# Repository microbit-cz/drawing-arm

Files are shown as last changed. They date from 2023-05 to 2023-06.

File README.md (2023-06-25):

## Language



Thingiverse: https://www.thingiverse.com/thing:6087701
Printables: https://www.printables.com/model/509500-microbit-robotic-drawing-arm-stardraw-megalink

# StardrawMegalink - Robotic drawing arm :tokyo_tower::mechanical_arm::clamp:

<div>
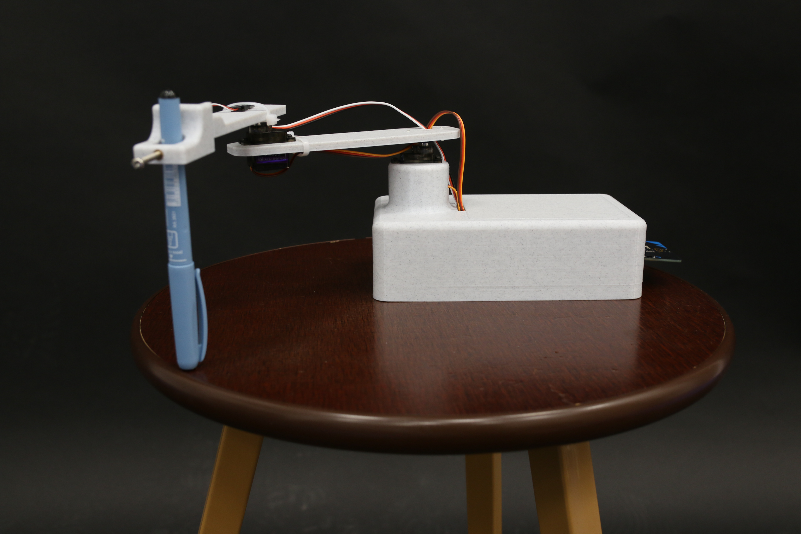
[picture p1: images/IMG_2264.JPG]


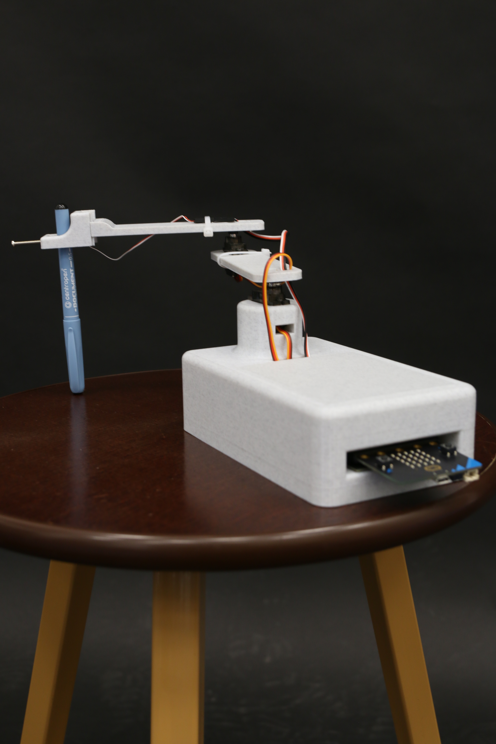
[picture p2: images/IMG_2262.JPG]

</div>

## Content

- [Introduction](#Introduction)
- [Equipment needed and price](#Equipment-needed)
- [Assembly and Printing](#Composition)
- [Software](#Software)

## Introduction
The project aims to create an experimental prototype of a drawing arm with a base. It is designed to test inverse kinematics. The software part is provided by a Micro:bit microcomputer with a library actually written for the digital servos controlling the arms.

## Equipment needed and price
- 3D printer with filament (recommended PLA) of about 400 grams with a print area of at least 18×18 cm **(price about 2 USD)**
- Nuts to load (12 nuts M14)
- 8 magnets (4 smaller: diameter 6 mm, thickness 1.3 mm, 4 larger: diameter 6 mm, thickness 2.6 mm) **(price approx. 2 USD)**
- Soldering iron 
- Instant glue
- 5× [thread inserts](https://eshop.sharplayers.cz/p/zavitove-vlozky-m3) **(price approx. 1 USD)**
- 2× [SG90 servo](https://www.aliexpress.com/item/4000903254039.html) **(price approx. 1.25 USD)**
- 2× Plastic handle for attaching the arm to the servo (included with the servo)
- Tiny linear [miniservo](https://www.aliexpress.com/item/1005004339409489.html) **(cena cca 8.5 USD)**
- [Micro:bit](https://www.amazon.com/GeeekPi-Micro-Original-Batteries-Programming/dp/B0BB6T186P/ref=sr_1_1_sspa)**(price approx. 34.5 USD)**
- [Expansion board for microbit
](https://www.aliexpress.com/item/32919813638.html) **(cena cca 11 USD)**
- Micro USB cable **(price approx. 1 USD)**
- [Micro USB adapter](https://www.aliexpress.com/item/1005002500157420.html) **(price approx. 2.1 USD)**
- Power cable extension tool and extension cable for microserv0o
 
***Total price: around 64.5 USD with micro:bit***

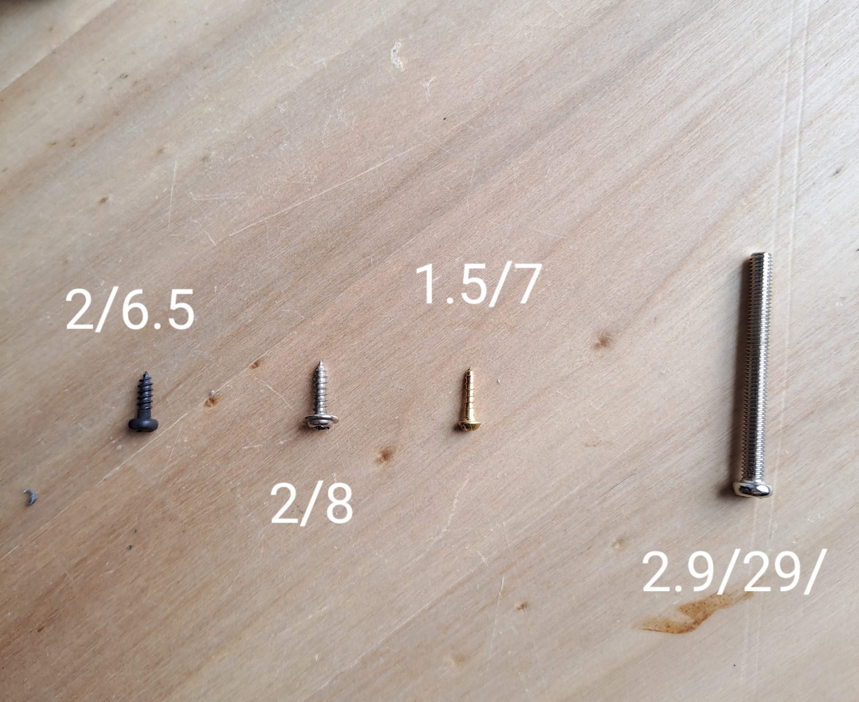
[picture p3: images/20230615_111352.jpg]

Similar screws and bolt must be obtained for assembly. Dimensions are given in width/length ratio (milimeters). The silver screw (second from the left) is supplied in the package with the servos.

## Assembly and printing

### Printing
Print the components below on a **3D printer**.
The recommended material for printing all components is **PLA**.

#### Arms
Links to download the arms in .STL format: [1st arm](./MODELS/models/STARDRAWMEGALINK_arm-1.STL), [2nd arm](./MODELS/models/STARDRAWMEGALINK_arm-2.STL).
If you need to customize the arms, they are also available in .SLDPRT format: [1st arm](./MODELS/solidworks_models/STARDRAWMEGALINK_arm-1.SLDPRT), [2nd arm](./MODELS/solidworks_models/STARDRAWMEGALINK_arm-2.SLDPRT).

#### Pen holder
Link to download the pen holder in .STL format: [Pen holder](./MODELS/models/STARDRAWMEGALINK_pen-grabber.stl).
If you need to customize the holder, the holder is also available in .SLDPRT format: [Pen holder](./MODELS/solidworks_models/STARDRAWMEGALINK_pen-grabber.SLDPRT).

#### Base with lid and cube for holding USB
Download links for base with lid and cube in .STL format: [Base](./MODELS/models/STARDRAWMEGALINK_base.STL), [Lid](./MODELS/models/STARDRAWMEGALINK_base--cover.STL), [Cube](./MODELS/models/STARDRAWMEGALINK_usb--block.STL). 
If you need to customize the arms, components in .SLDPRT format are also available: [Base](./MODELS/solidworks_models/STARDRAWMEGALINK_base.SLDPRT), [Lid](./MODELS/solidworks_models/STARDRAWMEGALINK_base--cover.SLDPRT), [Cube](./MODELS/models/STARDRAWMEGALINK_usb--block.SLDPRT).
**Beware!** it is necessary to set the breakpoint in your program controlling printing on the 3D printer to the position just before pressing the magnet insertion point and pressing the nut insertion point during printing.

<div>

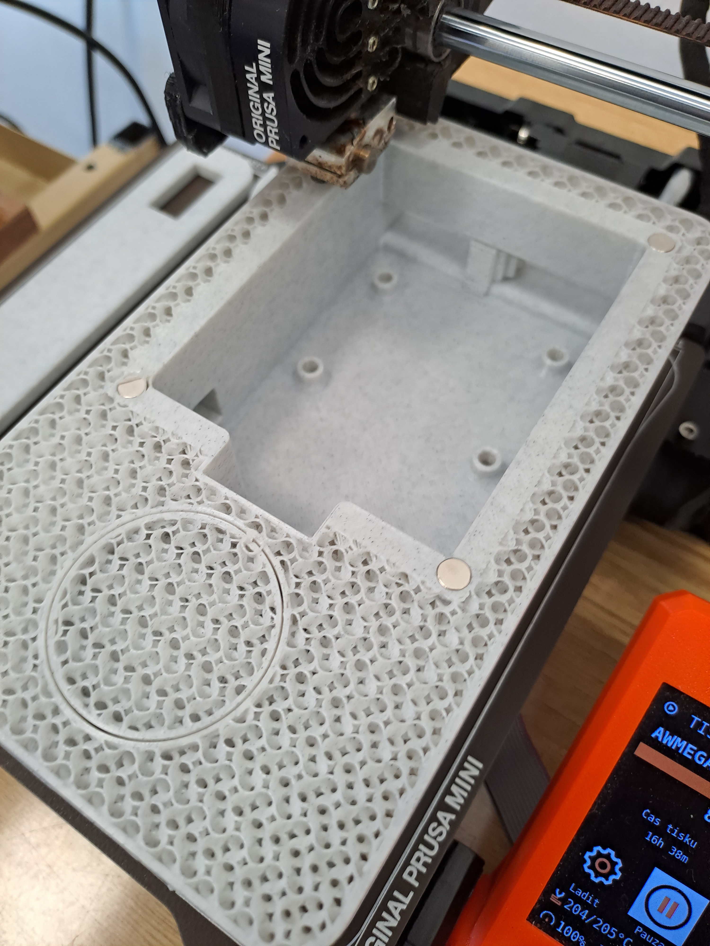
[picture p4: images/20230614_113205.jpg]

</div>

### Assembly
Once you have all the components printed, magnets and nuts embedded in the base, and all the parts secured, you can proceed to assembly.

#### 1. Soldering the threaded inserts
Heat the soldering iron to about 220 °C. Take the base and pen holder. Insert the threaded inserts into the holes in the base. One by one, place the tip of the soldering iron on each insert, waiting until the filament begins to melt slightly and the insert begins to embed. At this point, remove the soldering iron and push the insert into an aligned position using a blunt object (such as the end of a marker). Follow the same process for inserting the liner into the pen holder. **After embedding, wait at least 5 minutes to allow for setting**

<div>
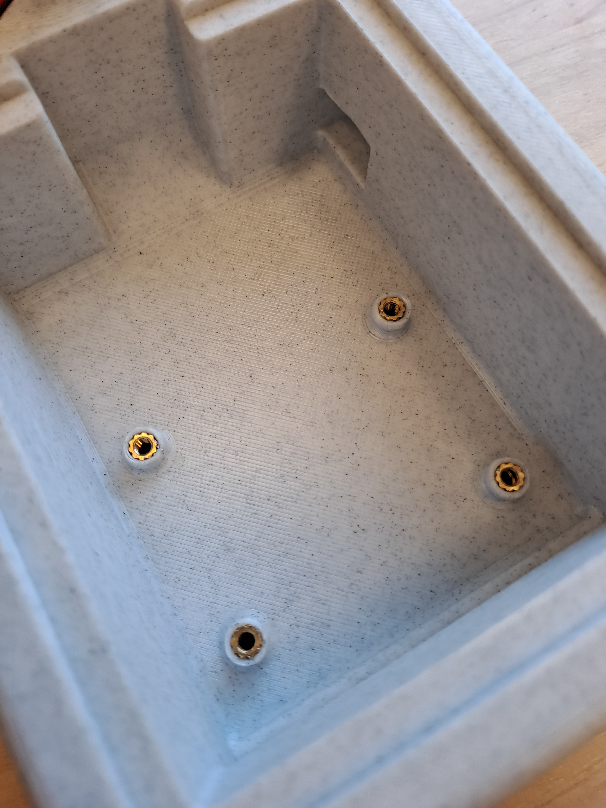
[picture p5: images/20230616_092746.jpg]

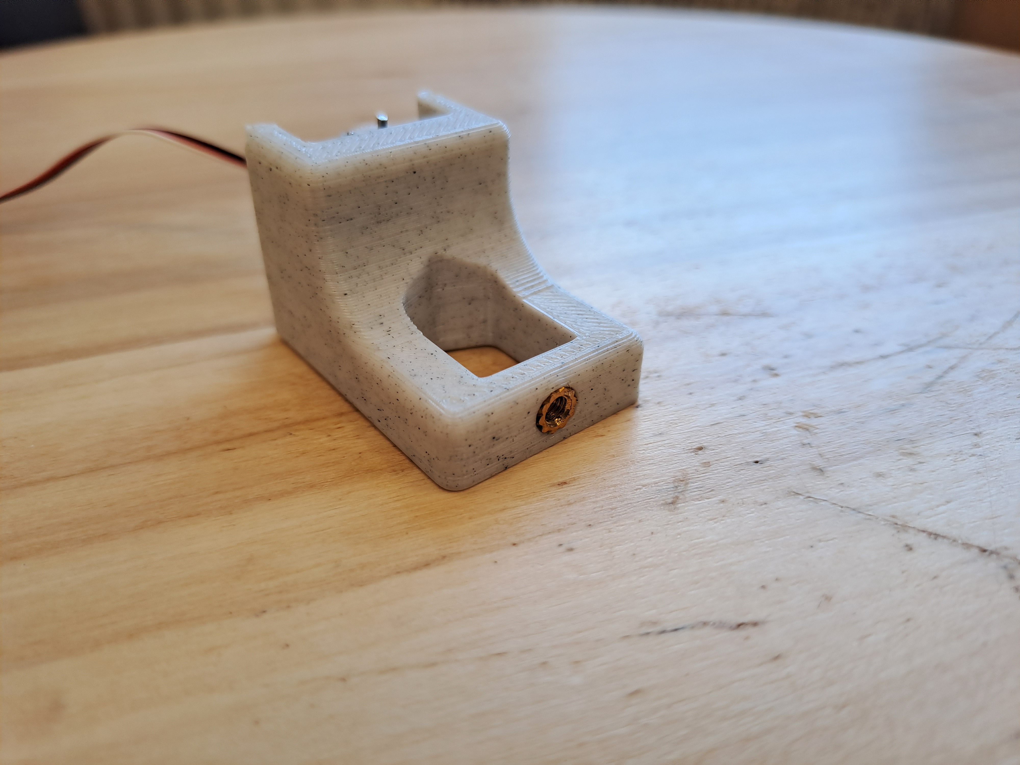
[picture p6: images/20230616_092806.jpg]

</div>

#### 2. Inserting the micro USB adapter
Insert the micro USB adapter into the hole on the inside of the base. Then take the printed cube, apply hot glue to the sides and slide the cube behind the micro USB adapter to fix the micro USB adapter in the hole.

<div>
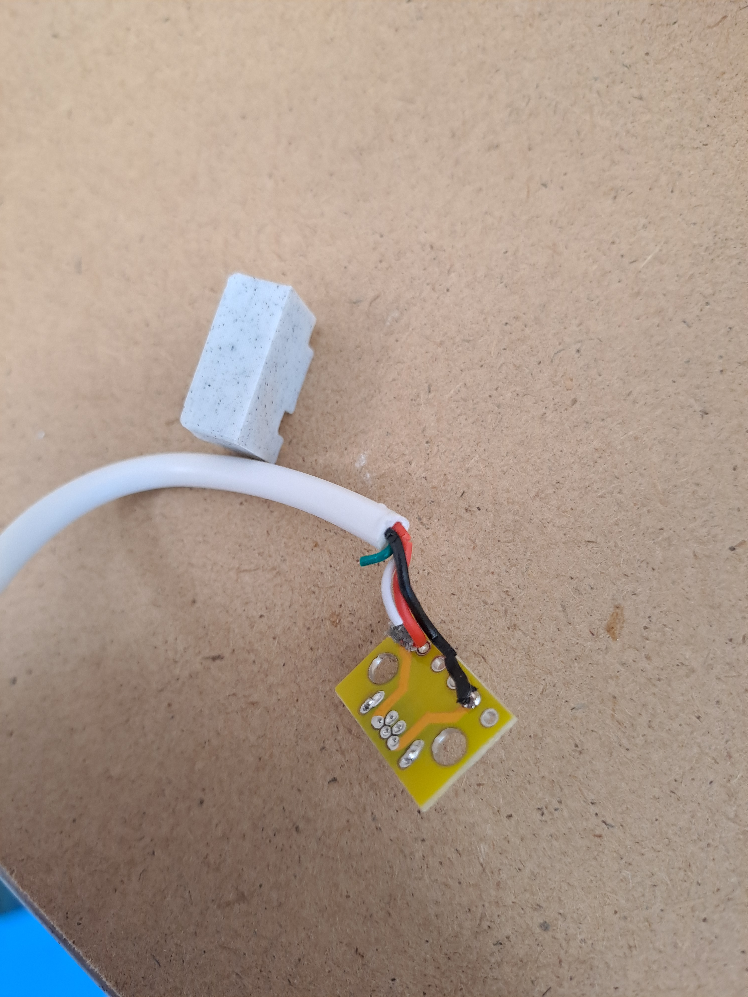
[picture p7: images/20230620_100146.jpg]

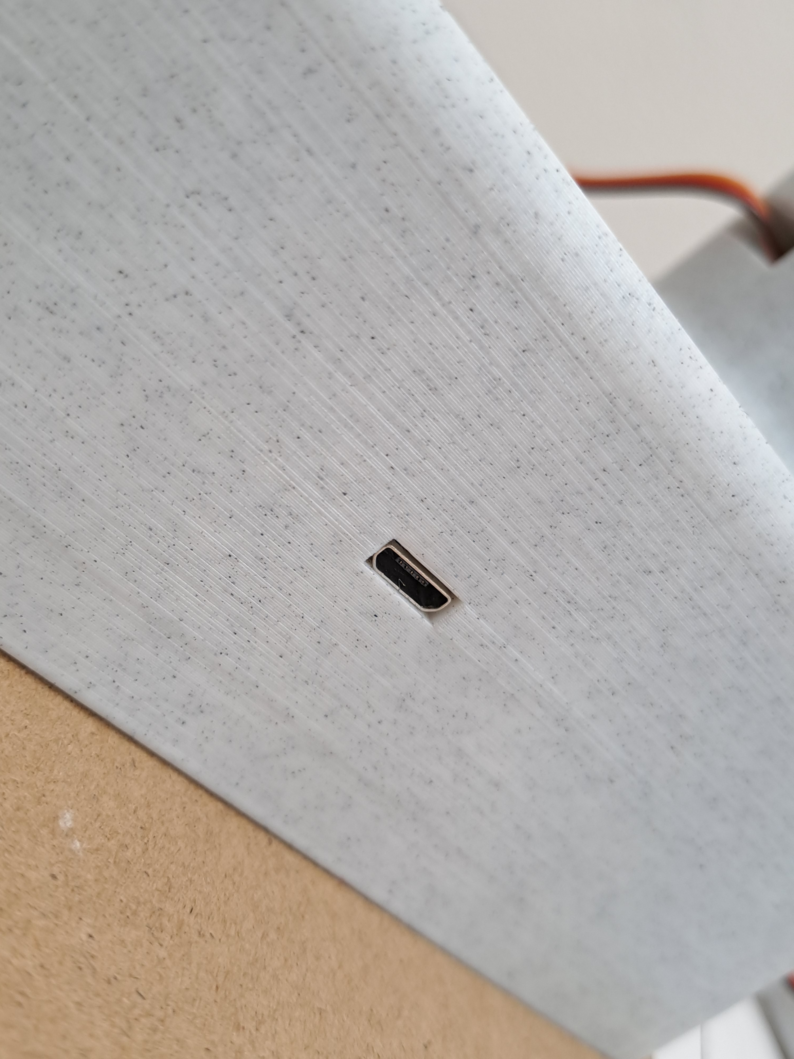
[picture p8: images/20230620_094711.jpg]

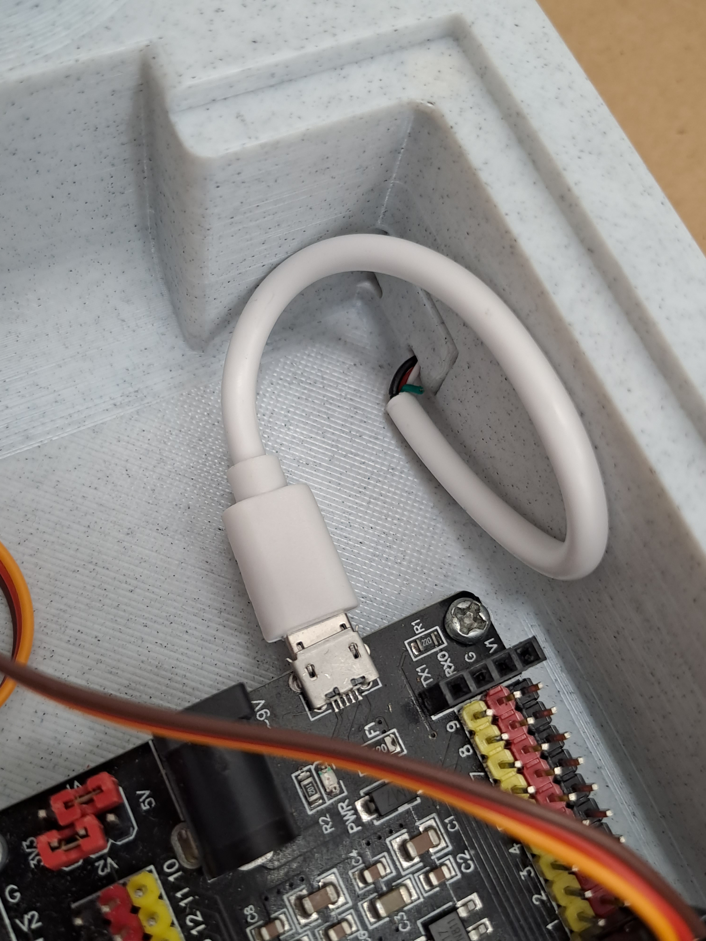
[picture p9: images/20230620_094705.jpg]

</div>

#### 3. Screwing in the micro:bit expansion board
Take the appropriate screws and screw the micro:bit expansion board to the base with them into the recessed inserts.

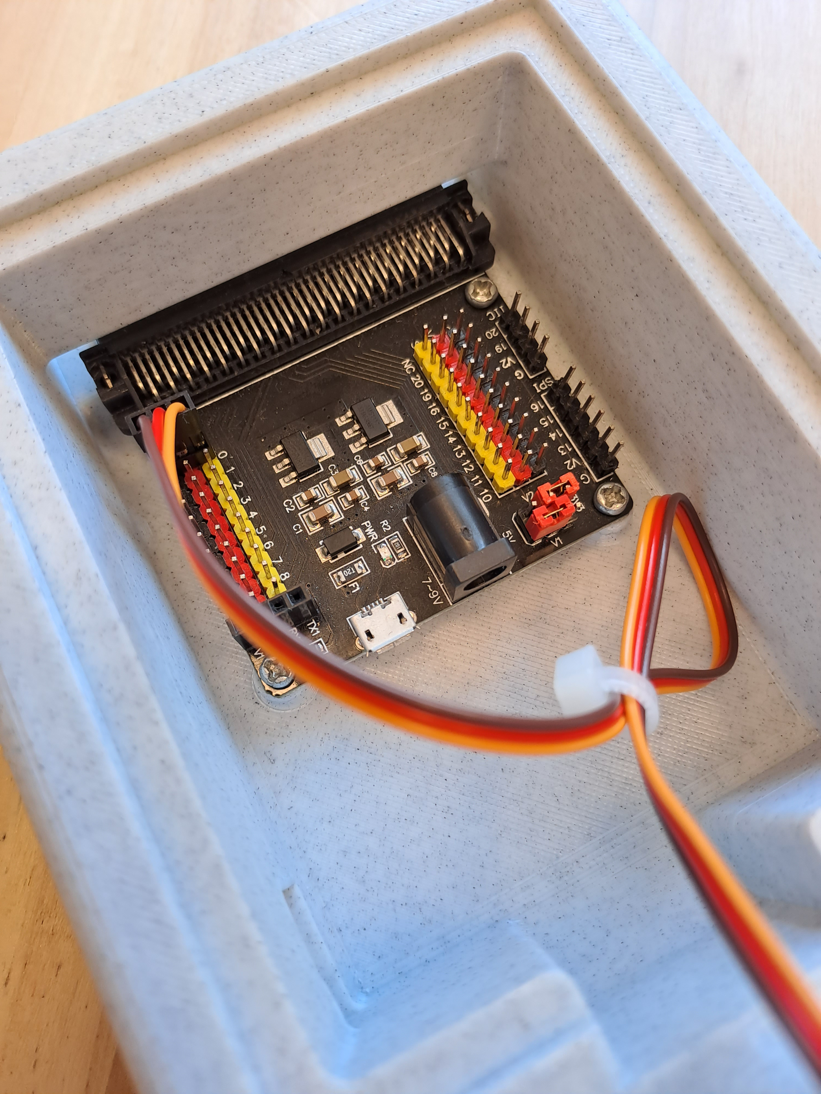
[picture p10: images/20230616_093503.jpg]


#### 4. Screw the servos into the base and arm
Take your servo motors and use the screws provided to screw one into the hole in the base. Screw the other servo motor into the hole in the arm 1.

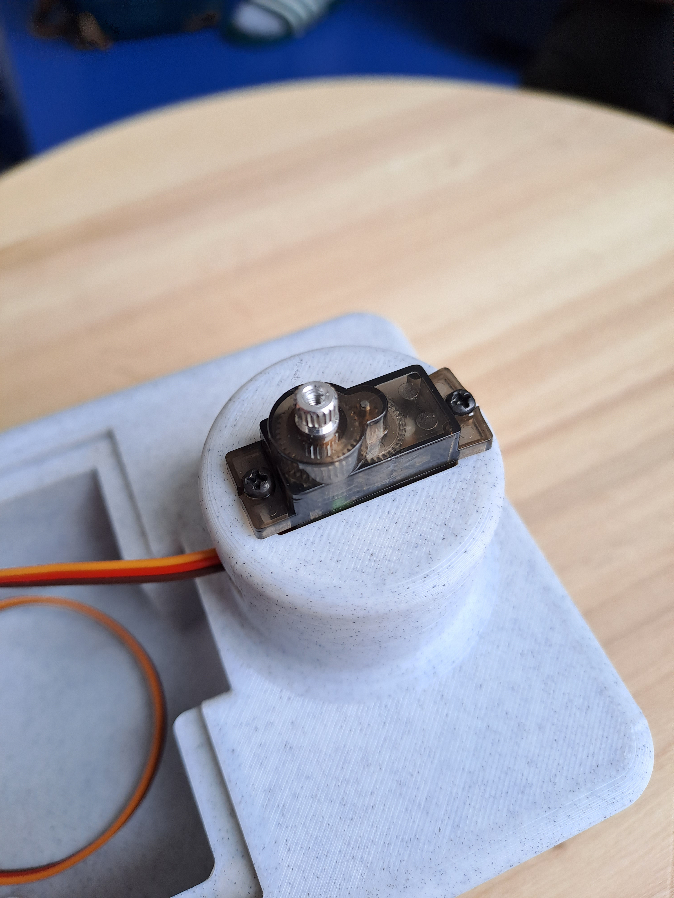
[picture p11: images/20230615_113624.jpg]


#### 5. Screwing in the linear motor
Take the linear motor and use the screws to screw it to the pen holder from the back side. Make sure that it is screwed in the direction shown in the picture.

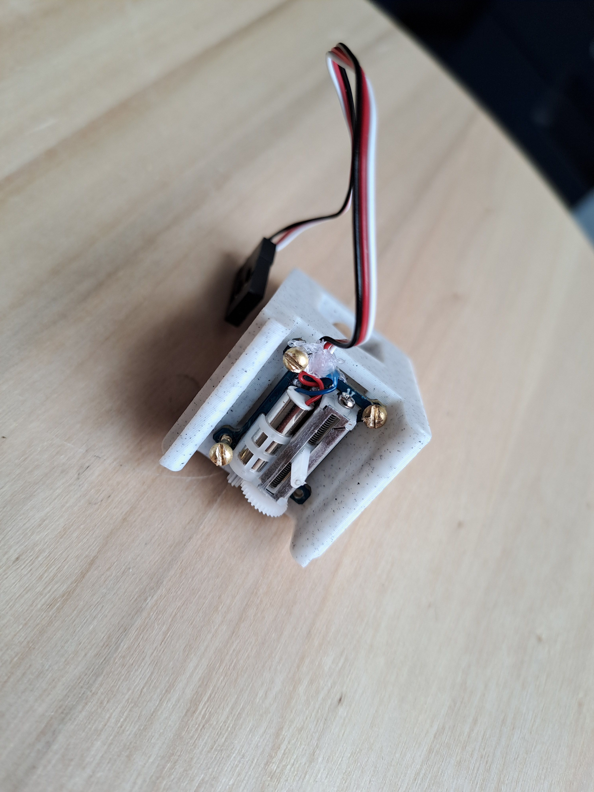
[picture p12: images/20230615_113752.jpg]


#### 6. Screwing on the servo handles
Screw the servo handles into the arm sockets using the screws provided.

<div>
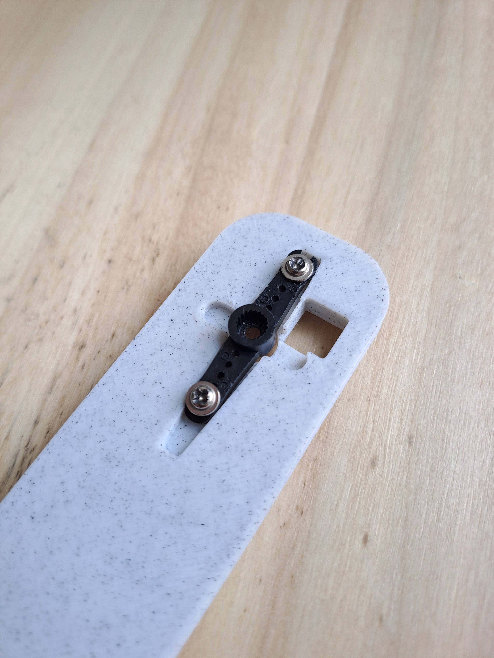
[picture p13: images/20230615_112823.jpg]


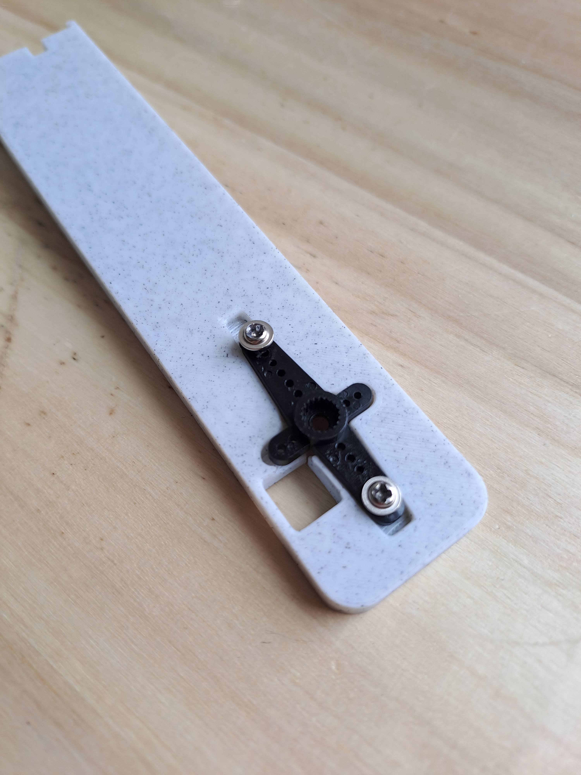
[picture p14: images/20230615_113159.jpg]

</div>

#### 7. Screw the arms together and to the base and add the pen holder
Screw the second arm to the servo on the first arm first using the included servo screw. Then screw the first arm to the servo in the base.
Also, add the pen holder to the second arm and drip hot glue between the tip of the linear servo and the second arm.


***Voila you have folded the robotic arm***

## Software
The software part is provided by the microsoft makecode environment for micro:bit https://makecode.microbit.org/.

An external [pxt-smooth-servo](https://github.com/Kraus-Ivan/pxt-smooth-servo) library written in *Typescript* was created for this project. The library provides servo and microservo control.
The library has its own documentation in the [main.ts](https://github.com/Kraus-Ivan/pxt-smooth-servo/blob/master/main.ts) code file.
The way to add this extension to the project's macrocode is described in [readme.md](https://github.com/Kraus-Ivan/pxt-smooth-servo/blob/master/README.md).
### Implementation of this class:

```typescript
basic.forever(function () {
    basic.pause(50);
	smoothServo.SmoothServo.update();
});

let servo1 = smoothServo.SmoothServo.createServo(AnalogPin.P0);
let servo2 = smoothServo.SmoothServo.createServo(AnalogPin.P1);

input.onButtonPressed(Button.A,() => {
    servo1.moveTo(2000);
    console.log(servo1.buffer());
    console.log(servo1.toString());
});
```

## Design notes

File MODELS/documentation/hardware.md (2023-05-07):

# Seznam použitého hardwaru
- 2x Micro servo MG90S s kovovými součástmi - link: [zde](https://www.amazon.com/ETMall-Helicopter-Arduino-Raspberry-Project/dp/B07R7PYK9T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)
- pravděpodobně KEYESTUDIO BBC Micro:bit Expansion Board Breakout Adapter Shield for BBC Micro bit Starter Kit Compatible with Microbit V2, V1 Controller Board(Without Microbit) - link: [zde](https://www.amazon.co.uk/keyestudio-Sensor-Shield-BBC-Micro/dp/B07H9X63CR?ref_=ast_sto_dp)
- malý servo motorek
- Micro:bit v2.2 - link: [zde](https://www.amazon.com/Microbit-Starter-Kit-Micro-Built/dp/B09MBBT9YL/ref=sr_1_5?keywords=microbit+v2&sr=8-5)

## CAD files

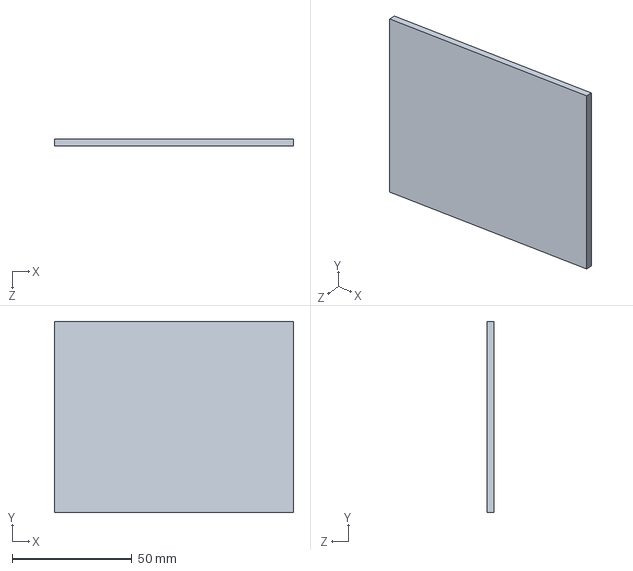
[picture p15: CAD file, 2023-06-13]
MODELS/solidworks_models/STARDRAWMEGALINK_base--cover.SLDPRT
100.0 x 80.0 x 3.00 mm

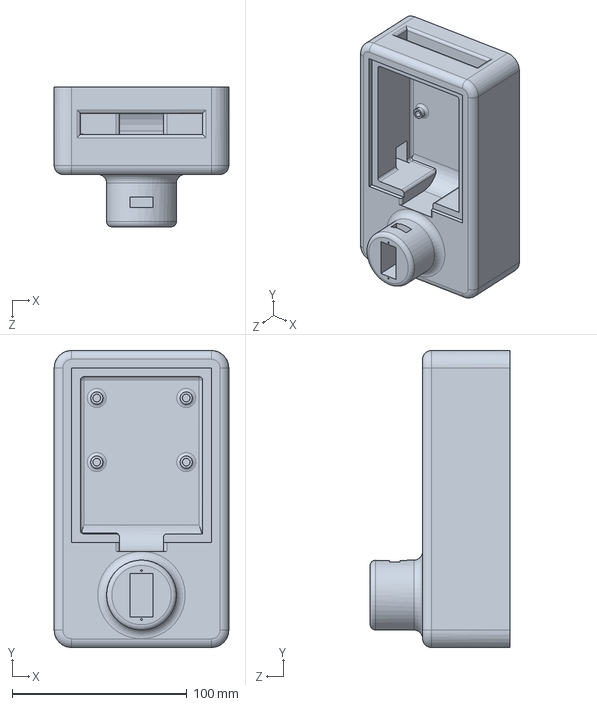
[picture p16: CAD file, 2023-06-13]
MODELS/solidworks_models/STARDRAWMEGALINK_base.SLDPRT
100.0 x 170.0 x 80.0 mm

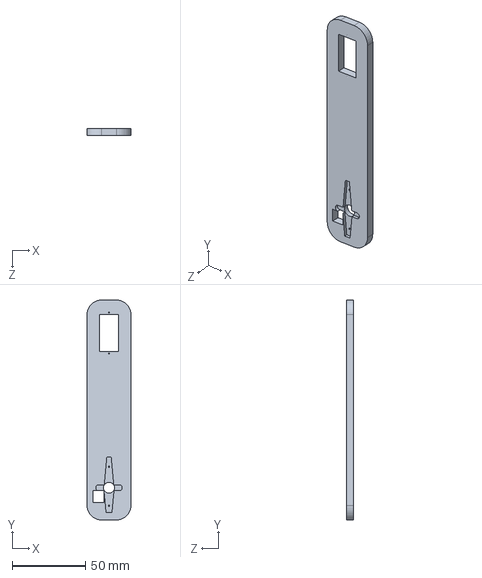
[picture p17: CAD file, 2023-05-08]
MODELS/solidworks_models/STARDRAWMEGALINK_arm-1.SLDPRT
30.0 x 150.0 x 5.00 mm

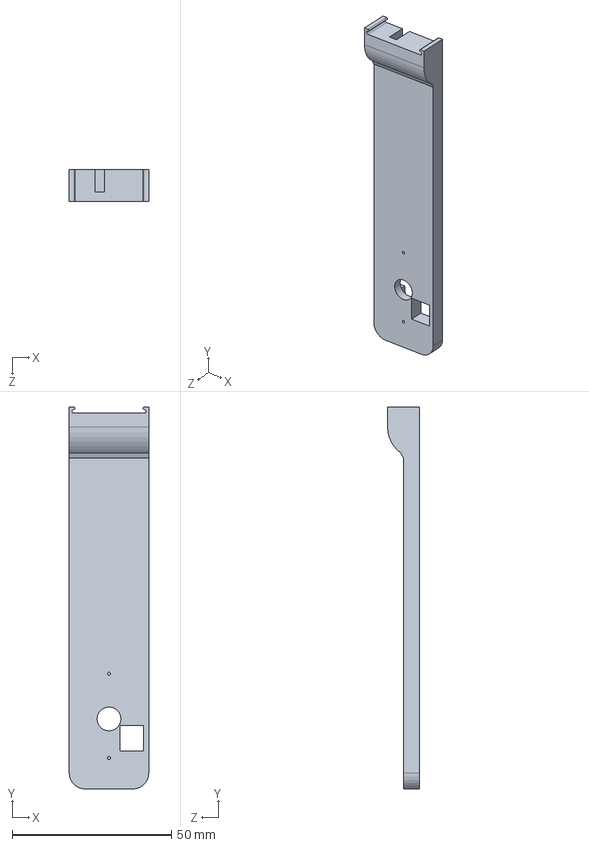
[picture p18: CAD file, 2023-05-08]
MODELS/solidworks_models/STARDRAWMEGALINK_arm-2.SLDPRT
25.0 x 120.0 x 10.0 mm

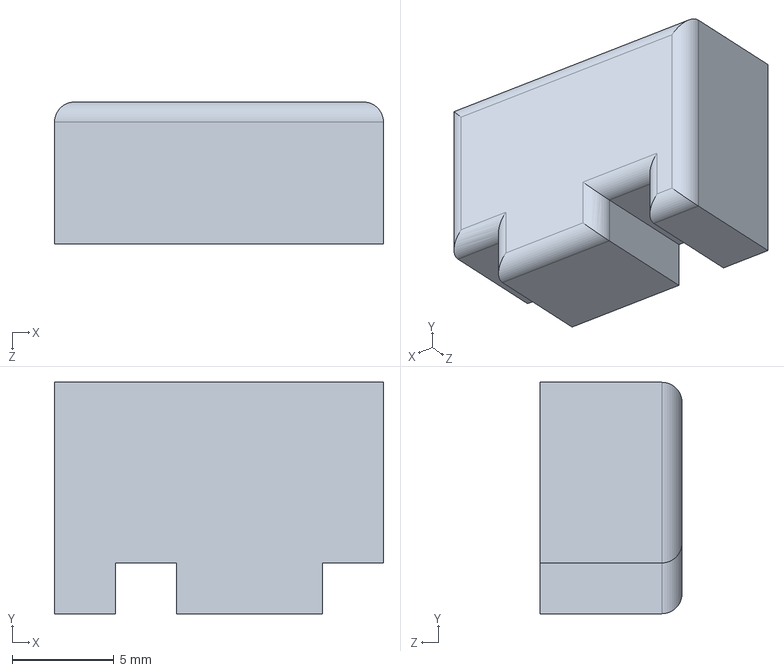
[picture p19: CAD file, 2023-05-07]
MODELS/solidworks_models/STARDRAWMEGALINK_usb--block.SLDPRT
16.2 x 11.4 x 7.00 mm

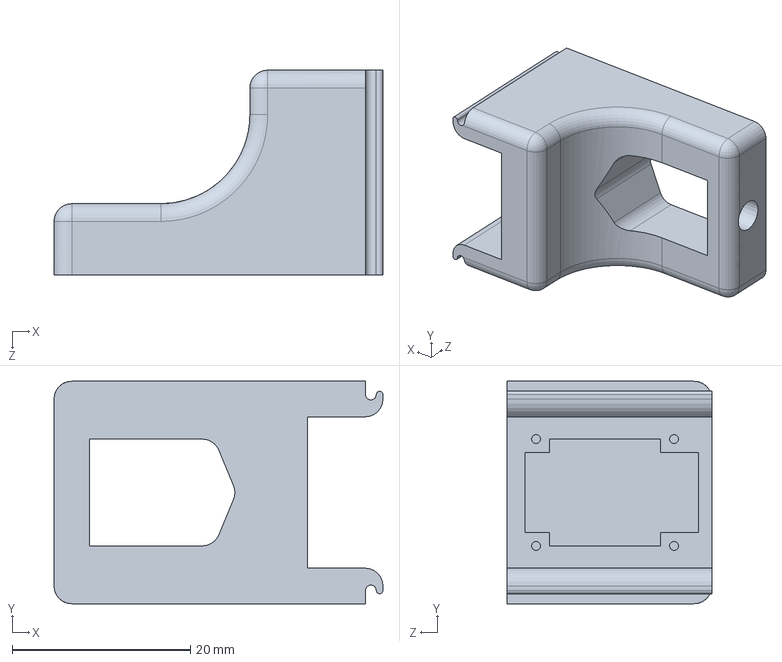
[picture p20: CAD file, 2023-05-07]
MODELS/solidworks_models/STARDRAWMEGALINK_pen-grabber.SLDPRT
37.0 x 25.0 x 23.0 mm

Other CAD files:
MODELS/models/STARDRAWMEGALINK_arm-1.STL
MODELS/models/STARDRAWMEGALINK_arm-2.STL
MODELS/models/STARDRAWMEGALINK_base--cover.STL
MODELS/models/STARDRAWMEGALINK_base.STL
MODELS/models/STARDRAWMEGALINK_pen-grabber.stl
MODELS/models/STARDRAWMEGALINK_usb--block.STL

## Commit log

2023-05-07 Models added
    [STARDRAWMEGALINK_ASSEMBLY.SLDASM, STARDRAWMEGALINK_arm-1.SLDPRT, STARDRAWMEGALINK_arm-1.STL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]
2023-05-08 Added díra ramena
    [STARDRAWMEGALINK_arm-1.STL, STARDRAWMEGALINK_arm-2.STL]
2023-05-08 Added zdířené ramena
    [STARDRAWMEGALINK_arm-1.SLDPRT, STARDRAWMEGALINK_arm-2.SLDPRT]
